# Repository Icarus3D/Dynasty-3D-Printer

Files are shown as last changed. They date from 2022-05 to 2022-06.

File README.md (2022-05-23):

# Dynasty CoreXY 3D Printer
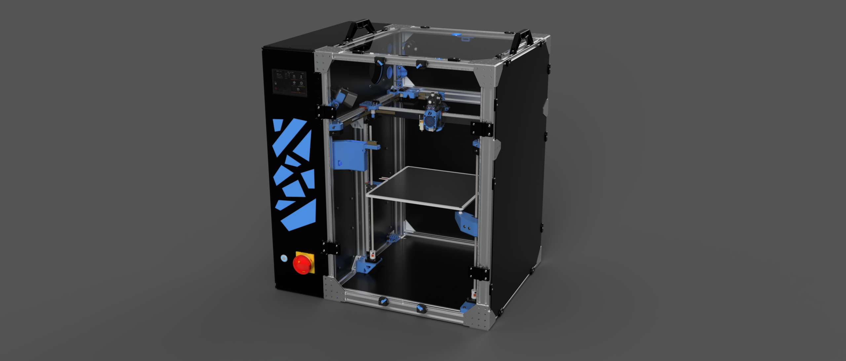
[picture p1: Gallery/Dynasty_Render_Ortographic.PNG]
Dynasty_Final_Render


After having modified my printers a lot and tested several DIY printer kits like Voron and BLV MGN Cube, I wanted a printer that totally met my needs.
I saw printers on the market that could correspond to my needs by modifying them. But I decided to challenge myself by developing my own printer.
After several months of work, here is the result.
This project was originally intended to be personal only, but I thought that making the files open source might motivate other people to start developing their own 3D printer.

:warning: Warning :warning:<br />
This printer is still at the prototype stage and is not optimized. The cost is quite high and the machine also takes a lot of space
If you want to build a 3D printer by yourself, I recommend the [Voron](https://www.vorondesign.com/) or [RatRig](https://v-core.ratrig.com/) printers which have a great community ready to help you.

If you are interested in my work, you can follow me on Instagram [@icarus_3d](https://www.instagram.com/icarus_3d/?hl=fr). I will post news about my future projects in 3D printing.

## Features List
* Print volume 300x300x360mm
* CoreXY kinematic
* Easy maintenance
* Sturdy Structure with 2040 Aluminium Profiles
* Good speed and print quality (Good result at 100mm/s @ 3k accel)
* Accepts spools of 2kg
* Electronic Bay
* Full enclosure
* Direct drive extruder
* Filament fault detector
* Purge Bucket
* Bed thermal expension compensation
* LED strip
* Auto bed leveling
* Access to the printer outside a local network
* Streaming video
* Timelapse
* Automatic power off after print completion

## Frame
Dynasty_3D_Printer
2040 aluminum profiles are used to obtain a rigid structure.
All corners use 3mm aluminum plates coupled with M6 screws directly screwed to the profiles as hidden joints.
The structure is very rigid, but it requires a lot of screws.
The printer, which is very heavy, is about 85cm high.
All electronic components are installed in the electronic bay on the left side of the printer. The panels on the front, bottom, top and back of the electronic bay are 3D printed.
The enclosure is made of transparent and matte black 3mm plexiglass. Except for the plate on which is fixed the electronics, which is 4mm thick.
Thanks to [coldzero.eu](https://www.coldzero.eu/) for the awesome [Custom Dynasty Panels Kit](https://www.coldzero.eu/custom-dynasty-panels).

## Motion System
Dynasty_XY_Carriage
The moving system is an XY core system. The two motors used for the movement of the print head are placed at the back of the printer.
The Y-axis uses two linear rails and the X-axis uses one linear rail fixed on a carbon tube.
The head is moved by a 9mm 2GT belt.

Dynasty_Hotend
The carriage of the hotend is an [EVA](https://main.eva-3d.page/). This is the same carriage platform used for the RatRig printers.

## Bed
Dynasty_Bed
The bed used is a 329x329x6mm cast tooling plate from RatRig.
There is a magnetic plate on top with a flexplate powder coated PEI.
The bed can be heated up to 110°C with a 750W heating pad.
It has three attachment points, each resting on a 3D printed support.
The fixation between the bed and the supports is made with steel balls screwed to the bed and attracted by magnets fixed on the supports.
This system allows to compensate the effects of the thermal expansion of the plate during the heating process. This avoids deformations of the bed caused by the stress. Steel rods guide the balls to ensure the stability of the bed.
The supports are screwed to linear rails and are moved by TR8 lead screws and Nema17 motors. 
These three motors, coupled with the BLTouch sensor, allow the automatic leveling of the bed . There is a link to a [video of the start gcode macro](https://www.youtube.com/watch?v=Yhw2lbUx1_E&t=1s).

## Electronics
Dynasty_Open_Bay
All the electronic components are installed in the electrical bay. Each component is fixed on a 35mm DIN rail with a bracket. The cables are all stored in a 40mm wiring duct.
The electrical bay allows easy access to all electronics and protects the components from the temperature of the printing area.
The printer has a 230V socket at the back. This is directly connected to the emergency stop button on the front panel.
The shutdown button is connected in parallel with the main SSR. Once the printer is switched on with the button, the SSR takes over and the printer can be switched off either via the web interface or directly with the emergency stop button.
The 24V power supply powers the Octopus V1.1 motherboard and the 5V power supply powers the Rapsberry Pi. Most of the components are connected to the motherboard except for the screen and the webcam. The details of the connections are explained in the [Wiring Diagram](https://github.com/Icarus3D/Dynasty-3D-Printer/tree/main/Wiring%20Diagram) folder.

## Firmware
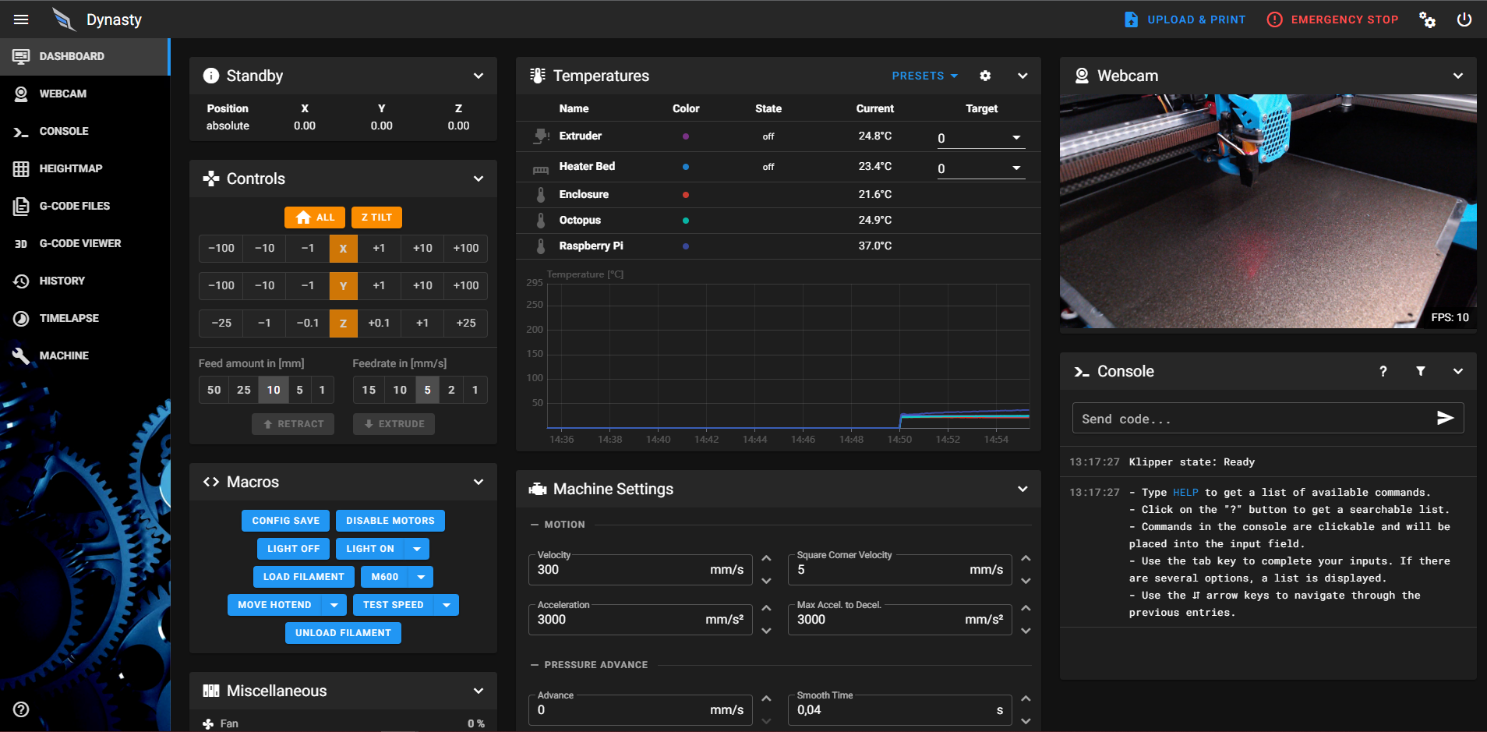
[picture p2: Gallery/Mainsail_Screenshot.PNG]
Mainsail_Screenshot

The printer uses the [Klipper firmware](https://github.com/Klipper3d/klipper).
You can use third-party Moonraker components that allow you to add other functionalities.
Like the [Moonraker timelapse](https://github.com/mainsail-crew/moonraker-timelapse) feature that allows you to make timelapse videos of your prints very easily. This feature was very useful for me to understand the failures of my first prints.
There is also a [Moonraker bot telegram](https://github.com/nlef/moonraker-telegram-bot) that allows you to regularly receive the status of the current print with an image or a short video. If the printing has failed, it is also possible to stop the printing. All this can be done outside the local network.
The user interface used is [Mainsail](https://github.com/mainsail-crew/mainsail). It's an excellent interface with a lot of features and is regularly updated.
All configuration files of the printer are available in the [Firmware](https://github.com/Icarus3D/Dynasty-3D-Printer/tree/main/Firmware) folder.

## Inspirations
The creation of the Dynasty printer was inspired by this open source printers. Thanks to their creator and their community.
* Voron Trident by Voron Design [Github](https://github.com/VoronDesign/Voron-Trident)<br />
* VzBot by Vez3D [Github](https://github.com/VzBoT3D/VzBoT-Vz330)<br />
* RatRig V-Core 3 by RatRig [Github](https://github.com/Rat-Rig/V-core-3)<br />
* BLV MGN Cube by Ben Levi [Web Site](https://www.blvprojects.com/blv-mgn-cube-3d-printer)<br />

## License
The Dynasty 3D printer uses the license [CC BY-NC-SA 4.0](https://creativecommons.org/licenses/by-nc-sa/4.0/)
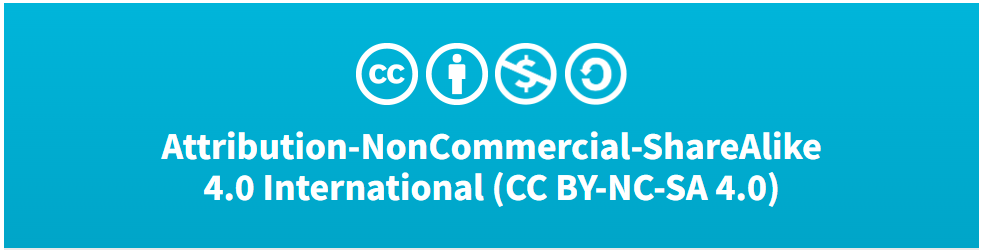
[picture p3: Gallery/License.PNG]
Dynasty_License


:exclamation: All 3D models created by other designers and their remixes used for this printer retain their original license. For more details, see the [3MFs STLs](https://github.com/Icarus3D/Dynasty-3D-Printer/tree/main/3MFs%20STLs) folder. :exclamation:

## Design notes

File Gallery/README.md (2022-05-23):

# Gallery

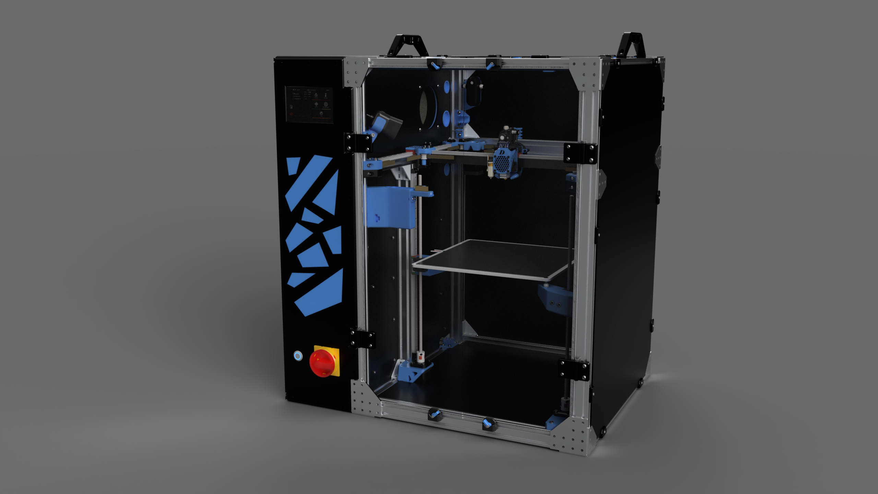
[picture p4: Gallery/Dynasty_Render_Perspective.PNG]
Dynasty_Render_Perspective


Dynasty_Banana_for_Scale

Dynasty_Vase_Mode

[Armadillo Timelapse Video](https://www.youtube.com/watch?v=8Uq6_T-8N7Q)
Armadillo_Print_Sample

[DesertKiss Timelapse Video](https://www.youtube.com/watch?v=NnbRvlF1Fk8)
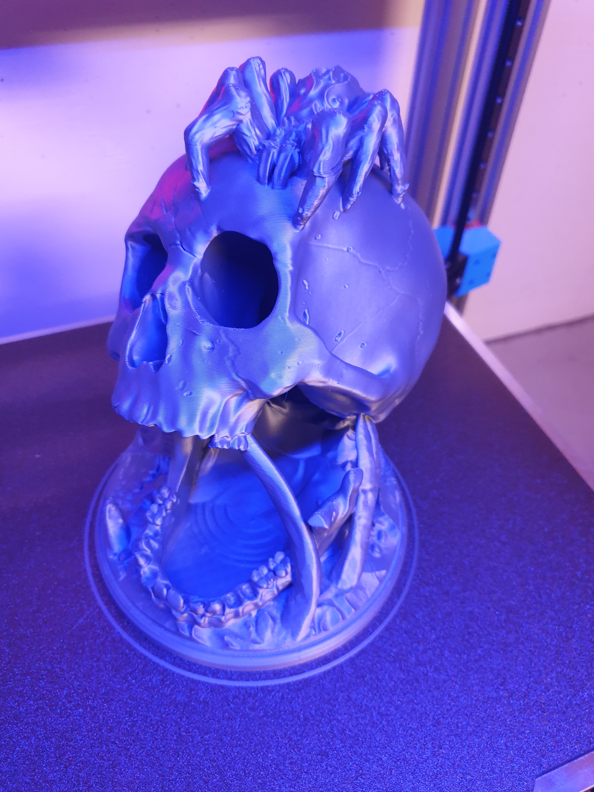
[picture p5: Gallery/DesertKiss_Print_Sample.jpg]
DesertKiss_Print_Sample


[ElfBust Timelapse Video](https://www.youtube.com/shorts/Z34vOpA37Mc)
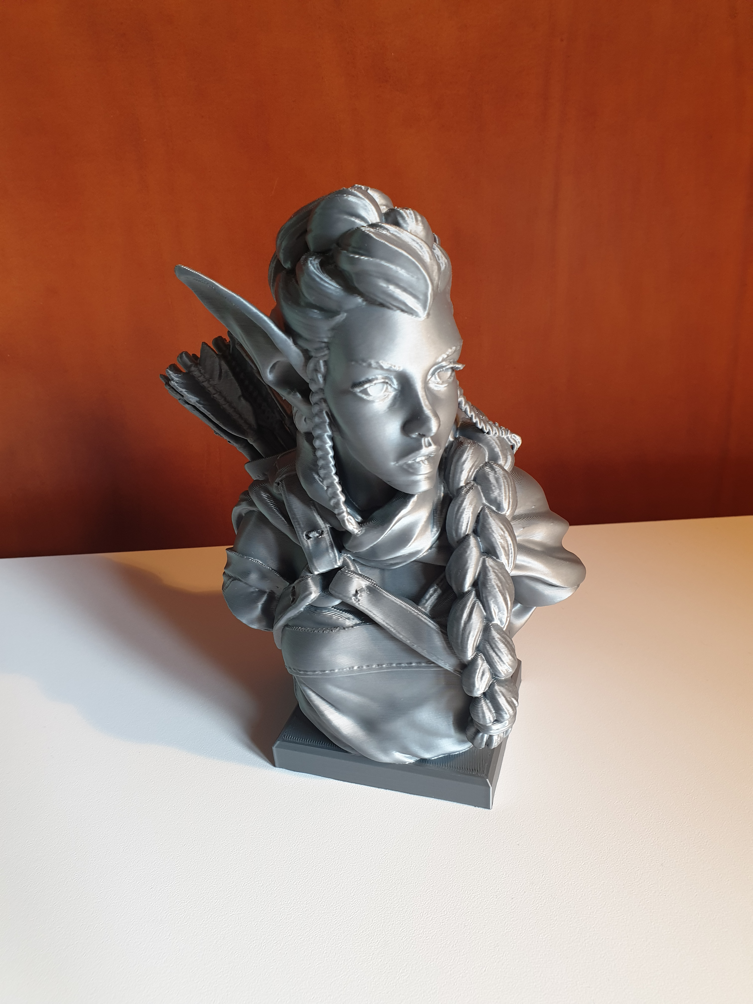
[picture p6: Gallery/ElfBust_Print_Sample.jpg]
ElfBust_Print_Sample


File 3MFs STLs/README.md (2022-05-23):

# .3MF & .STL Files
All files are available in .3MF and .STL format.
Files with the prefix "a_" are printed with the secondary color. Blue is the secondary color of the reference model.
Some files that need to be printed several times have the number of units to be printed as a suffix, for example "_x2".
It is recommended to print the parts used inside the enclosure in ABS or any other equivalent plastic. Other parts that are not sensitive to temperature can be printed in PLA or PETG.
Grommets are the exception. They are printed in TPU A95 to be flexible enough to let the cables pass through.

This printer uses parts made by other designers. Here is a list of these pieces with the details of their remix.
All these files keep their original license.

## DIN Rail Bracket
* a_DIN_Rail_Bracket_Clip_08_Dynasty_Remix_x6.stl<br />
This is a small remix of the [LM2596 Buck Converter Din Bracket](https://www.thingiverse.com/thing:4820100) originally created by 100k3y.
The original was not tight enough on the rail and the brackets were moving along the DIN rail when the printer was moved. To correct this, the distance between the two brackets was reduced by 0.8mm.

## Exhaust Fan Case
* a_fancase-server-bottom-fan-housing.stl
* a_fancase-server-grille.stl
* fancase-server-filter-section.stl<br />
The exhaust fan case [3D Enclosure Extractor Fan with HEPA Carbon filters v2](https://www.printables.com/fr/model/54864-3d-enclosure-extractor-fan-with-hepa-carbon-filter) was made by Colin.
I did not change anything in the original files. I modeled two printed seals in TPU to have a better airtightness.

## Spool Holder
* a_FillerGuideSource_Dynasty_Remix.stl
* a_FillerRollerSource_Dynasty_Remix.stl
* a_FillerWallMountSource_Dynasty_Remix.stl<br />
Remix from the [Filler - The Customizable Filament Holder that fills your printer!](https://www.thingiverse.com/thing:3020026) originally created by HugoHuge.
The roller and the guide has been enlarged to fit a 2.3kg filament spool.
The wall mount has also been modified so that it can be attached to the aluminum profile and panel without touching the other components.

## Door latch
* a_Enclosure_Latch_Left_Dynasty_Remix_x2.stl
* a_Enclosure_Lever_Left_Dynasty_Remix_x2.stl
* Enclosure_Lock_Body_Left_Dynasty_Remix_x2.stl
* a_Enclosure_Latch_Right_Dynasty_Remix_x2.stl
* a_Enclosure_Lever_Right_Dynasty_Remix_x2.stl
* Enclosure_Lock_Body_Right_Dynasty_Remix_x2.stl<br />
This latch originally come from VoronDesign. Unfornately, I have never found the orginals files of VoronDesign. I got them from the VzBot .step files by Vez3D.
The side in contact with the plexiglass door has been enlarged to ensure better adhesion. The shape has been slightly modified to match the size of Motedis aluminum profiles.

## Panel Clip
* Midspan_Panel_Clip_3mm_Dynasty_Remix_x28.stl
* Midspan_Panel_Clip_4mm_Dynasty_Remix_x10.stl<br />
Originals files [midspan_panel_clip_3mm_x12.stl](https://github.com/VoronDesign/Voron-1/blob/Voron1.8/STLs/Panel_Mounting/midspan_panel_clip_3mm_x12.stl) were made by VoronDesign.
The 3mm version has been slightly modified to have a tighter fit and does not touch the 3D printed panels of the electronic bay.
The 4mm version is based on the 3mm and used for the 4mm electronic panel. The dimensions have been adapted for the 4mm panel and prevent the clip from touching the 3D printed panels.

## Handle
* VzBoT_Handle_Dynasty_Remix_x2.stl<br />
Remix of VzBot handle [handle.stl](https://github.com/VzBoT3D/VzBoT-Vz330/blob/master/Assemblies%20BOM%20and%20STL/Frame/STLs/handle.stl) originally created by Vez3D.
The handles have been raised a few millimeters to facilitate access to the handles near the panels.

## Hotend
* a_shroud_dynasty_remix.stl
* top_orbiter_mgn12_dynasty_remix.stl
* etc...<br />
All the files of the 3D carriage platform of this printer were created by the [EVA](https://main.eva-3d.page/) team.
A grid has been added to the shroud to protect the fan. The edges have been shortened to allow the addition of an ADXL345 accelerometer. 
Two holes were added to the top orbiter mgn12 to put two M2.5 inserts wich allow to fix the accelerometer.

## Wires Holder
* Frame_Wires_Holder.stl<br />
This [Frame Wires Holder](https://www.blvprojects.com/post/beta-test-frame-wires-holder) were made by Ben Levi.
They have not been modified.

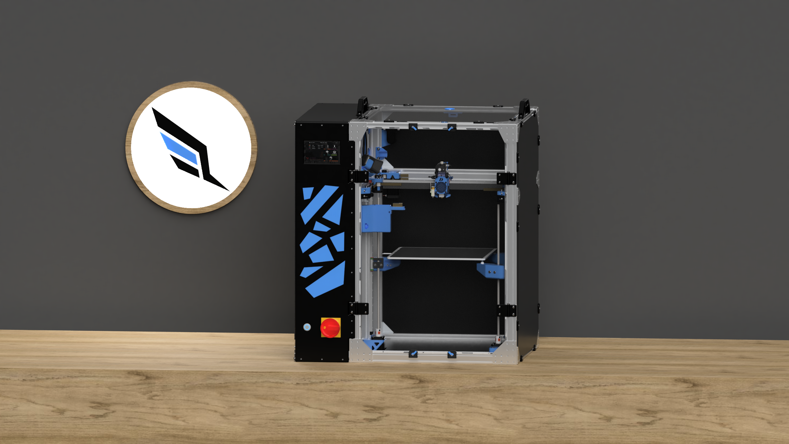
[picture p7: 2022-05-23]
Gallery/Dynasty_Scene_Ortographic2.PNG

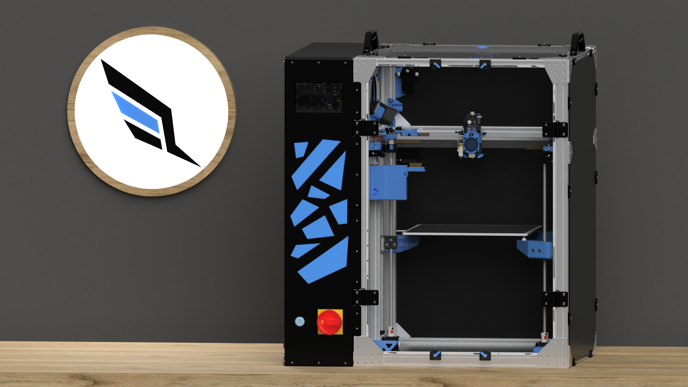
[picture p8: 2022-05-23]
Gallery/Dynasty_Scene_Ortographic.PNG

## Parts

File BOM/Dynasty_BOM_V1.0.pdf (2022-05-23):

Dynasty_BOM_Rev1.0

Page 1

Category | Subcategory | Component | Quantity | Price per Unit | Price | Link
Printed Parts | Filament | Primary Color (Black) | 1 | 28.40 USD | 28.40 USD | Fiberlogy ABS+ (https://www.3djake.ch/fr-CH/fiberlogy/abs-plus-black)
| | Secondary Color (Blue) | 1 | 28.40 USD | 28.40 USD | Fiberlogy ABS+ (https://www.3djake.ch/fr-CH/fiberlogy/abs-plus-blue)
Frame | Structure | Aluminum Profile 2020 Type B Slot 6 180mm | 4 | 1.06 USD | 4.24 USD | Motedis (https://www.motedis.ch/shop/Profile-a-rainures/Profile-aluminium-20x20-Type-B-rainure-6::999991.html)
| | Aluminum Profile 2040 Type B Slot 6 480mm | 5 | 4.82 USD | 24.10 USD | Motedis (https://www.motedis.ch/shop/Profile-a-rainures/Profile-aluminium-20x40-Type-B-rainure-6::99999158.html)
| | Aluminum Profile 2040 Type B Slot 6 520mm | 6 | 5.22 USD | 31.32 USD | Motedis (https://www.motedis.ch/shop/Profile-a-rainures/Profile-aluminium-20x40-Type-B-rainure-6::99999158.html)
| | Aluminum Profile 2040 Type B Slot 6 530mm | 2 | 5.32 USD | 10.64 USD | Motedis (https://www.motedis.ch/shop/Profile-a-rainures/Profile-aluminium-20x40-Type-B-rainure-6::99999158.html)
| | Aluminum Profile 2040 Type B Slot 6 800mm | 4 | 8.03 USD | 32.12 USD | Motedis (https://www.motedis.ch/shop/Profile-a-rainures/Profile-aluminium-20x40-Type-B-rainure-6::99999158.html)
| Feet | Threaded Rod M6x40 for Ball Feet, Steel, Series 10 | 4 | 1.12 USD | 4.48 USD | Motedis (https://www.motedis.ch/shop/Base-mechaniques/Pieds-reglables-et-accessoires/Pied-reglable-en-piece-detachee/Articles-Elements-etage-serie-10-PA/Articles-Eleme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)
| | Base 40 for Adjustable Feet, PA, Series 10 | 4 | 1.43 USD | 5.71 USD | Motedis (https://www.motedis.ch/shop/Base-mechaniques/Pieds-reglables-et-accessoires/Pied-reglable-en-piece-detachee/Articles-Elements-etage-serie-10-PA/Articles-Eleme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)
| | Anti-slip Plate 40 for Adjustable Feet, Series 10 | 4 | 1.27 USD | 5.07 USD | Motedis (https://www.motedis.ch/shop/Base-mechaniques/Pieds-reglables-et-accessoires/Pied-reglable-en-piece-detachee/Articles-Elements-etage-serie-10-PA/Articles-Eleme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)
| Plate | Plate L 2020 3mm 5 Holes | 4 | 1.16 USD | 4.63 USD | Motedis (https://www.motedis.ch/shop/Profile-accessoires/Plaques-de-connexion/Plaque-de-connexion-en-L-58x58x3-Decoupe-au-laser::999993868.html)
| | Plate L 2040 4mm 7 Holes | 8 | 0.96 USD | 7.68 USD | Aliexpress (https://fr.aliexpress.com/item/32649078057.html?cn=e-c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)
| | Plate L 4040 3mm 12 Holes | 8 | 1.57 USD | 12.60 USD | Motedis (https://www.motedis.ch/shop/Profile-accessoires/Plaques-de-connexion/Plaque-de-connexion-en-L-78x78x3-Decoupe-au-laser::999993853.html)
| | Plate T 2020 3mm 5 Holes | 4 | 1.16 USD | 4.63 USD | Motedis (https://www.motedis.ch/shop/Profile-accessoires/Plaques-de-connexion/Plaque-de-connexion-en-T-58x58x3-Decoupe-au-laser-serie-20::999993776.html)
| | Plate T 4040 3mm 12 Holes | 2 | 1.54 USD | 3.09 USD | Motedis (https://www.motedis.ch/shop/Profile-accessoires/Plaques-de-connexion/Plaque-de-connexion-en-T-78x78x3-Decoupe-au-laser::999993857.html)
| Bracket | Bracket 2020 B-Type Slot 6 (with fixing kit) | 13 | 1.44 USD | 18.72 USD | Motedis (https://www.motedis.ch/shop/Profile-accessoires/Bracket-for-Aluminium-profiles/Equerre-dassemblage-20x20-B-type-rainure-6::999991062.html)
| | Bracket 2040 B-Type Slot 6 (with fixing kit) | 19 | 2.37 USD | 45.03 USD | Motedis (https://www.motedis.ch/shop/Profile-accessoires/Bracket-for-Aluminium-profiles/Equerre-dassemblage-20x40-B-type-rainure-6::99999554.html)
| Panels | Dynasty Panels Kit 3mm & 4mm | 1 | 220.10 USD | 220.10 USD | Coldzero (https://www.coldzero.eu/custom-dynasty-panels)
Motion System | XY axe | Carbon fiber tube 20x20x18 500mm | 1 | 11.50 USD | 11.50 USD | Aliexpress (https://fr.aliexpress.com/item/32946654825.html?spm=a2g0s.9042311.0.0.3e6e6c37yhnRV5)
| | MGN12H 400mm linear rail Z1 preloaded block | 3 | 65.00 USD | 195.00 USD | Aliexpress (https://www.aliexpress.com/item/4000799585801.html?spm=a2g0o.cart.0.0.68773c00W9mmQ3&mp=1)
| | | 1 | 18.80 USD | 18.80 USD
| | Idler Pulley - Smooth for 2GT-20T - 9mm Belt - 5mm Bore (Compressible) | 8 | 4.30 USD | 34.40 USD | RatRig (https://www.ratrig.com/idler-pulley-gt-20t-profile-smooth-multiple-sizes-and-types.html)
| | Idler Pulley - Toothed for 2GT-20T - 9mm Belt - 5mm Bore (Compressible) | 2 | 4.45 USD | 8.90 USD | RatRig (https://www.ratrig.com/idler-pulley-toothed-for-2gt-20t-5mm-bore-multiple-sizes-and-types.html)
| | Timing Pulley - 2GT (2mm) - 20 Tooth - For 9mm Belt | 2 | 2.16 USD | 4.32 USD | RatRig (https://www.ratrig.com/openbuilds-gt2-2mm-aluminum-timing-pulley-9mm.html)
| | High Torque Nema17 Motor 0.9° | 5 | 15.92 USD | 79.60 USD | E3D (https://e3d-online.com/products/motors)
| Z axe | MGN12H 450mm linear rail Z1 preloaded block | 3 | 71.40 USD | 214.20 USD | Aliexpress (https://www.aliexpress.com/item/4000799585801.html?spm=a2g0o.cart.0.0.68773c00W9mmQ3&mp=1)
| | Lead Screw Flexible Coupler | 3 | 4.87 USD | 14.61 USD | Aliexpress (https://fr.aliexpress.com/item/33011094528.html)
| | Lead Screw T8 PTFE 450mm | 3 | 16.84 USD | 50.52 USD | Aliexpress (https://fr.aliexpress.com/item/1005002055526955.html)
| | Anti-Backlash Nut Block for 8mm Lead Screw | 3 | 5.79 USD | 17.37 USD | RatRig (https://www.ratrig.com/anti-backlash-nut-block-for-8mm-metric-acme-lead-screw.html)
| | Thrust Bearing F8-16M | 3 | 1.83 USD | 5.49 USD | RatRig (https://www.ratrig.com/thrust-bearing-f8-16m.html)
| Bed | FlexPlate Powder Coated PEI 310x310mm | 1 | 51.98 USD | 51.98 USD | RatRig (https://www.ratrig.com/flexplate-set-pei-310-x-310-mm.html)
| | Bed Plate 329*329*6mm | 1 | 58.68 USD | 58.68 USD | RatRig (https://www.ratrig.com/bed-plate-cast-tooling-plate-pre-machined-multiple-sizes.html)
| | Aluminium Spacer 6mm | 3 | 0.24 USD | 0.72 USD | RatRig (https://www.ratrig.com/aluminium-spacer-6mm.html)
| | Steel Ball 12mm M5 | 3 | 1.05 USD | 3.15 USD | RatRig (https://www.ratrig.com/steel-ball-12mm-threaded-m5.html)
| | Dowel Pin 3x35mm | 6 | 0.42 USD | 2.52 USD | RatRig (https://www.ratrig.com/dowel-pin-3-0mm-x-35-0mm.html)
| | Magnet 20x10x5mm Two hole M3 | 3 | 2.10 USD | 6.30 USD | RatRig (https://www.ratrig.com/magnet-20-x-10-x-5mm-two-hole-m3-countersink-screws.html)
Electric | Hotend | Dragon High Flow Hotend | 1 | 80.11 USD | 80.11 USD | Aliexpress (https://fr.aliexpress.com/item/1005002629698126.html)
| | Orbiter Extruder V1.5 | 1 | 55.18 USD | 55.18 USD | Aliexpress (https://fr.aliexpress.com/item/1005002029267359.html?spm=a2g0s.9042311.0.0.3e6e6c37yhnRV5)
| | Sunon 4010 12V Fan | 1 | 4.62 USD | 4.62 USD | Digikey (https://www.digikey.ch/product-detail/fr/MF40101VX-1000U-A99/259-1798-ND/6198736?itemSeq=373298864)
| | Sunon 5015 12V Fan | 1 | 8.51 USD | 8.51 USD | Digikey (https://www.digikey.ch/product-detail/fr/sunon-fans/MF50151VX-B00U-A99/259-1829-ND/7691033)
| | Heater Cartridge 24V 40W | 1 | 1.94 USD | 1.94 USD | Aliexpress (https://fr.aliexpress.com/item/32815934251.html)
| | Semitec 104GT-2 ATC thermistor | 2 | 2.34 USD | 4.68 USD | Aliexpress (https://fr.aliexpress.com/item/32847452724.html)
| | Omron Endstop | 2 | 2.98 USD | 5.96 USD | Digikey (https://www.digikey.ch/de/products/detail/omron-electronics-inc-emc-div/SS-5GL2/137204)
| | BLTouch | 1 | 42.10 USD | 42.10 USD | 3Djake (https://www.3djake.ch/fr-CH/antclabs/capteur-de-nivellement-bltouch)
| | Accelerometer ADXL345 | 1 | 21.00 USD | 21.00 USD | Distrelec (https://www.distrelec.ch/fr/adxl345-trois-axes-capteur-acceleration-5v-adafruit-1231/p/30139029)
| | PFA Tube 2m | 1 | 8.84 USD | 8.84 USD | Aliexpress (https://fr.aliexpress.com/item/33030078259.html)
| Bed | C-LIN SSR 40A | 1 | 22.01 USD | 22.01 USD | RatRig (https://www.ratrig.com/clin-ssr-40a-relay.html)
| | Silicone Heater Bed Pad 280x280mm 220V 600W | 1 | 66.50 USD | 66.50 USD | RatRig (https://www.ratrig.com/keenovo-heater-pad-and-ssr-relays-multiple-sizes-configurations.html)
| | Thermal Fuse 15A 125°C | 1 | 3.09 USD | 3.09 USD | Aliexpress (https://fr.aliexpress.com/item/32885492280.html)
| Electronics | Shurter Plug C14 250V | 1 | 4.36 USD | 4.36 USD | Distrelec (https://www.distrelec.ch/fr/fiche-pour-appareils-c14-250v-schurter-6200-2200/p/14358747)
| | Metal Switch 22mm 220V Self-Reset | 1 | 3.33 USD | 3.33 USD | Aliexpress (https://fr.aliexpress.com/item/4001246312476.html)
| | Cable Socket 22mm | 1 | 1.14 USD | 1.14 USD | Aliexpress (https://fr.aliexpress.com/item/4001291947746.html)
| | Eaton Emergency Switch | 1 | 41.93 USD | 41.93 USD | Distrelec (https://www.distrelec.ch/fr/interrupteur-principal-arret-urgence-eaton-t0-8200-ea-svb/p/13511931)
| | Crouzet SSR 50A | 1 | 56.88 USD | 56.88 USD | Digikey (https://www.digikey.ch/de/products/detail/crouzet/84137120N/13175957)
| | CUI Inc. 24V Power Supply VGS-320D-24-B | 1 | 55.55 USD | 55.55 USD | Digikey (https://www.digikey.ch/de/products/detail/cui-inc/VGS-320D-24-B/13690525)
| | DC/DC Converter DIN Rail 5V 3A | 1 | 25.09 USD | 25.09 USD | Distrelec (https://www.distrelec.ch/fr/convertisseur-dc-dc-pour-rail-din-5v-3a-15w-reglable-mean-well-ddr-15g/p/30134120)
| | BTT Octopus V1.1 Motherboard with TMC2209 | 1 | 67.63 USD | 67.63 USD | Aliexpress (https://fr.aliexpress.com/item/1005002611654405.html)

## Bill of Materials for Dynasty 3D Printer [V1.0 10.05.2022]

Belt 2GT 9mm – 600mm | RatRig (https://www.ratrig.com/gt2-timing-belt-1mt.html) | Aliexpress (https://fr.aliexpress.com/item/32853559638.html)

Dynasty_BOM_Rev1.0

Page 2

| | Younuon 6010 Fan 24V | 1 | 8.97 USD | 8.97 USD | Aliexpress (https://fr.aliexpress.com/item/4000233226859.html)
| | BTT Smart Filament Sensor | 1 | 11.52 USD | 11.52 USD | Aliexpress (https://fr.aliexpress.com/item/4000269547406.html)
| | Noctua NF-F12 iPPC-2000 | 1 | 34.50 USD | 34.50 USD | LDLC (https://www.ldlc.com/fr-ch/fiche/PB00169917.html)
| | Hepa Cover Filter Set Zortrax | 1 | 36.85 USD | 36.85 USD | 3Djake (https://www.3djake.ch/fr-CH/zortrax/hepa-cover-filter-set)
| | LED Strip RGBNW 1m 60 IP65 White PCB | 1 | 9.37 USD | 9.37 USD | Aliexpress (https://fr.aliexpress.com/item/32476317187.html?mp=1)
| | Raspberry Pi 3 B+ | 1 | 43.42 USD | 43.42 USD | Mouser (https://www.mouser.ch/ProductDetail/Raspberry-Pi/RPI3-MODBP-BULK?qs=gTYE2QTfZfTS/nQn9798dg==)
| | Winsinn 4010 fan 24V | 1 | 2.41 USD | 2.41 USD | Aliexpress (https://fr.aliexpress.com/item/1005003878405207.html)
| | 0.5m USB Cable | 1 | 2.69 USD | 2.69 USD | Aliexpress (https://fr.aliexpress.com/item/32678087225.html)
| | Flexible Cable 1m Raspebrry Pi | 1 | 0.53 USD | 0.53 USD | Aliexpress (https://fr.aliexpress.com/item/1005001636578419.html)
| | BTT PI TFT50 Screen | 1 | 47.15 USD | 47.15 USD | Aliexpress (https://fr.aliexpress.com/item/1005001270623489.html)
| | Logitech Streamcam | 1 | 125.00 USD | 125.00 USD | Digitec (https://www.digitec.ch/fr/s1/product/logitech-streamcam-2-mpx-webcams-12926543?supplier=406802)
| | Adapter USB 3.0 to USB-C | 1 | 9.20 USD | 9.20 USD | Digitec (https://www.digitec.ch/fr/s1/product/exsys-ex-47991-usb-30-370-cm-adaptateurs-pour-notebook-6037208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)
| Mounting | Wiring Duct 40x40mm 2m | 1 | 16.05 USD | 16.05 USD | Distrelec (https://www.distrelec.ch/fr/chemins-de-cables-heladuct-40-40mm-2m-pvc-gris-hellermanntyton-htwd-pw-40x40-pvc-gy/p/30119358)
| | Rail DIN omega 1m 35x7.5mm | 2 | 4.50 USD | 9.00 USD | Distrelec (https://www.distrelec.ch/fr/rail-din-omega-1m-35x7-5mm-rnd-connect-rnd-465-00766/p/30119896)
| | SSR DIN Rail Clamp | 2 | 2.26 USD | 4.52 USD | Aliexpress (https://fr.aliexpress.com/item/32865553893.html?mp=1)
| | Self-closing braided wire sheath | 2 | 2.70 USD | 5.40 USD | Aliexpress (https://fr.aliexpress.com/item/4000284383278.html)
| | Bearing 608 | 1 | 5.01 USD | 5.01 USD | Aliexpress (https://fr.aliexpress.com/item/32956652613.html?pdp_ext_f=%7B%22sku_id%22:%2266485988816%22%7D)
Fasterners | Set | Set Insert M2,M3,M4,M5 | 1 | 11.33 USD | 11.33 USD | Aliepxress (https://fr.aliexpress.com/item/4000023033943.html)
| | Set M3 SHCS Screws & Nuts | 1 | 17.82 USD | 17.82 USD | Aliexpress (https://fr.aliexpress.com/item/4001345484717.html)
| | Set M2,M3,M4,M5 BHCS Screws, Shim & Nuts 880 | 1 | 24.54 USD | 24.54 USD | Aliexpress (https://fr.aliexpress.com/item/33033655207.html)
| | Set M2,M3,M4,M5 SHCS Screws, Shim & Nuts 880 | 1 | 25.66 USD | 25.66 USD | Aliexpress (https://fr.aliexpress.com/item/33033655207.html)
| | Set M2,M3,M4,M5 FHCS Screws, Shim & Nuts 880 | 1 | 23.43 USD | 23.43 USD | Aliexpress (https://fr.aliexpress.com/item/33033655207.html)
| M2 | M2x10 SHCS | 2 | 0.64 USD | 1.28 USD | Aliexpress (https://fr.aliexpress.com/item/33046502668.html)
| | | 12 | 0.00 USD | 0.00 USD
| | | 3 | 0.00 USD | 0.00 USD
| | | 2 | 0.00 USD | 0.00 USD
| | M3x8 SHCS | 134 | 0.14 USD | 18.14 USD | Motedis (https://www.motedis.ch/shop/Base-mechaniques/DIN-standard-elements/Vis-DIN-7380::999991070.html)
| | M3x10 SHCS | 8 | 0.00 USD | 0.00 USD | Set M3 SHCS Screws & Nuts
| | M3x12 SHCS | 32 | 0.05 USD | 1.63 USD | Aliexpress (https://fr.aliexpress.com/item/33046502668.html)
| | M3x16 SHCS | 12 | 0.00 USD | 0.00 USD | Set M3 SHCS Screws & Nuts
| | M3x20 SHCS | 12 | 0.00 USD | 0.00 USD | Set M3 SHCS Screws & Nuts
| | M3x30 SHCS | 2 | 0.00 USD | 0.00 USD | Set M3 SHCS Screws & Nuts
| | M3x40 SHCS | 12 | 0.00 USD | 0.00 USD | Set M3 SHCS Screws & Nuts
| | | 3 | 0.00 USD | 0.00 USD
| | | 2 | 0.00 USD | 0.00 USD
| | M3 T Nut | 148 | 0.05 USD | 6.85 USD | Aliexpress (https://fr.aliexpress.com/item/32814359094.html)
| | | 30 | 0.00 USD | 0.00 USD
| | | 8 | 0.00 USD | 0.00 USD
| | | 4 | 0.00 USD | 0.00 USD
| | | 4 | 0.00 USD | 0.00 USD
| | | 8 | 0.00 USD | 0.00 USD
| | | 12 | 0.00 USD | 0.00 USD
| M5 | M5x8 BHCS | 300 | 0.14 USD | 40.62 USD | Motedis (https://www.motedis.ch/shop/Base-mechaniques/DIN-standard-elements/Vis-DIN-7380::999991070.html)
| | M5x10 BHCS | 34 | 0.14 USD | 4.60 USD | Motedis (https://www.motedis.ch/shop/Base-mechaniques/DIN-standard-elements/Vis-DIN-7380::999991070.html)
| | M5x12 BHCS | 20 | 0.14 USD | 2.71 USD | Motedis (https://www.motedis.ch/shop/Base-mechaniques/DIN-standard-elements/Vis-DIN-7380::999991070.html)
| | M5x16 BHCS | 22 | 0.14 USD | 2.98 USD | Motedis (https://www.motedis.ch/shop/Base-mechaniques/DIN-standard-elements/Vis-DIN-7380::999991070.html)
| | | 4 | 0.00 USD | 0.00 USD
| | M5x16 SHCS | 16 | 0.16 USD | 2.60 USD | Motedis (https://www.motedis.ch/shop/Base-mechaniques/DIN-standard-elements/Vis-DIN-912::999991121.html)
| | | 5 | 0.00 USD | 0.00 USD
| | M5x30 SHCS | 8 | 0.16 USD | 1.30 USD | Motedis (https://www.motedis.ch/shop/Base-mechaniques/DIN-standard-elements/Vis-DIN-912::999991121.html)
| | M5x35 SHCS | 2 | 0.16 USD | 0.32 USD | Motedis (https://www.motedis.ch/shop/Base-mechaniques/DIN-standard-elements/Vis-DIN-912::999991121.html)
| | M5x40 SHCS | 10 | 0.16 USD | 1.62 USD | Motedis (https://www.motedis.ch/shop/Base-mechaniques/DIN-standard-elements/Vis-DIN-912::999991121.html)
| | M5x45 SHCS | 8 | 0.16 USD | 1.30 USD | Motedis (https://www.motedis.ch/shop/Base-mechaniques/DIN-standard-elements/Vis-DIN-912::999991121.html)
| | | 4 | 0.00 USD | 0.00 USD
| | | 18 | 0.00 USD | 0.00 USD
| | M5 T Nut B-Slot Type 6 | 424 | 0.19 USD | 80.35 USD | Motedis (https://www.motedis.ch/shop/Profile-accessoires/Dans-la-rainure/Ecrou-a-tete-marteau-B-Type-rainure-6-M5::999997145.html)
| | | 43 | 0.00 USD | 0.00 USD
| | Mini Precision Shim M5 | 20 | 0.26 USD | 5.20 USD | RatRig (https://www.ratrig.com/precision-mini-shim-8x5x1mm.html)
| M6 | M6x16 BHCS | 48 | 0.14 USD | 6.50 USD | Motedis (https://www.motedis.ch/shop/Base-mechaniques/DIN-standard-elements/Vis-DIN-7380::999991070.html)
| | | | Total: | 2,501.83 USD
M3 | M3x8 BHCS | Set M2,M3,M4,M5 BHCS Screws, Shim & Nuts
| M3x12 BHCS | Set M2,M3,M4,M5 BHCS Screws, Shim & Nuts
| M3x20 BHCS | Set M2,M3,M4,M5 BHCS Screws, Shim & Nuts
| M3x12 FHCS | Set M2,M3,M4,M5 FHCS Screws, Shim & Nuts 880
| M3x20 FHCS | Set M2,M3,M4,M5 FHCS Screws, Shim & Nuts 880
| M3 Nut | Set M2,M3,M4,M5 SHCS Screws, Shim & Nuts 880
M4 | M4x12 BHCS | Set M2,M3,M4,M5 BHCS Screws, Shim & Nuts 880
| M4x20 BHCS | Set M2,M3,M4,M5 BHCS Screws, Shim & Nuts 880
| M4x8 SHCS | Set M2,M3,M4,M5 SHCS Screws, Shim & Nuts 880
| M4 Shim | Set M2,M3,M4,M5 SHCS Screws, Shim & Nuts 880
| M4 Nut | Set M2,M3,M4,M5 SHCS Screws, Shim & Nuts 880
M5x12 SHCS | Set M2,M3,M4,M5 SHCS Screws, Shim & Nuts 880
M5x20 SHCS | Set M2,M3,M4,M5 SHCS Screws, Shim & Nuts 880
M5x16 FHCS | Set M2,M3,M4,M5 FHCS Screws, Shim & Nuts 880
M5 Shim | Set M2,M3,M4,M5 SHCS Screws, Shim & Nuts 880
M5 Nut | Set M2,M3,M4,M5 SHCS Screws, Shim & Nuts 880

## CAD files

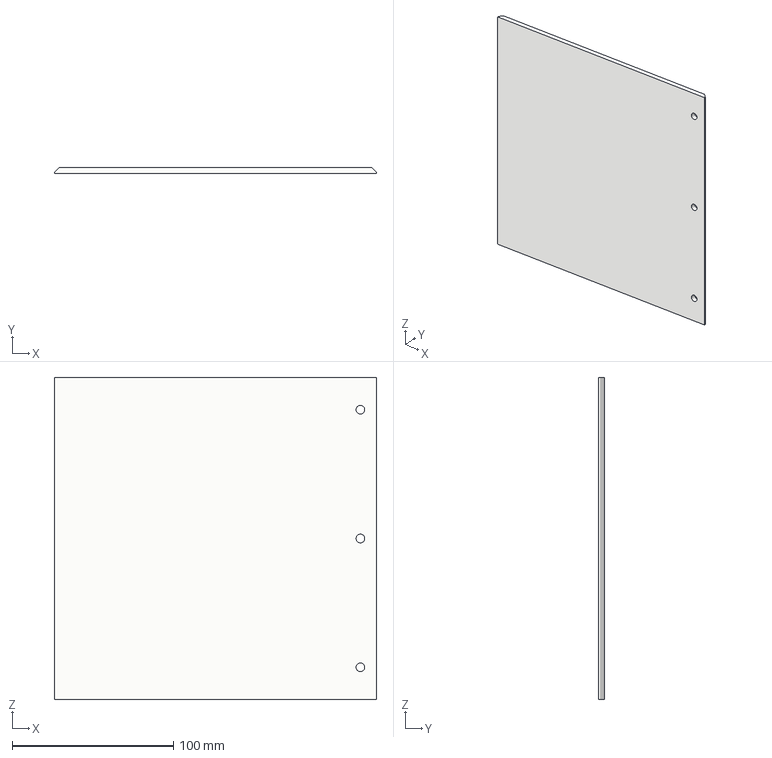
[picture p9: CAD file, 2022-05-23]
3MFs STLs/Electronics_Bay/3D_Panel/Back_3D_Panel/Back_3D_Panel_Part3.3mf
200.0 x 4.00 x 200.0 mm

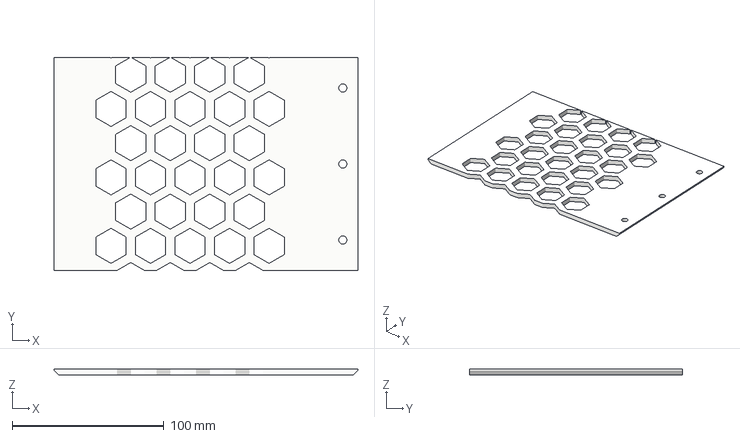
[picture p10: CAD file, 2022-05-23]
3MFs STLs/Electronics_Bay/3D_Panel/Bot_3D_Panel/Bot_3D_Panel_Part2.3mf
200.0 x 140.0 x 4.00 mm

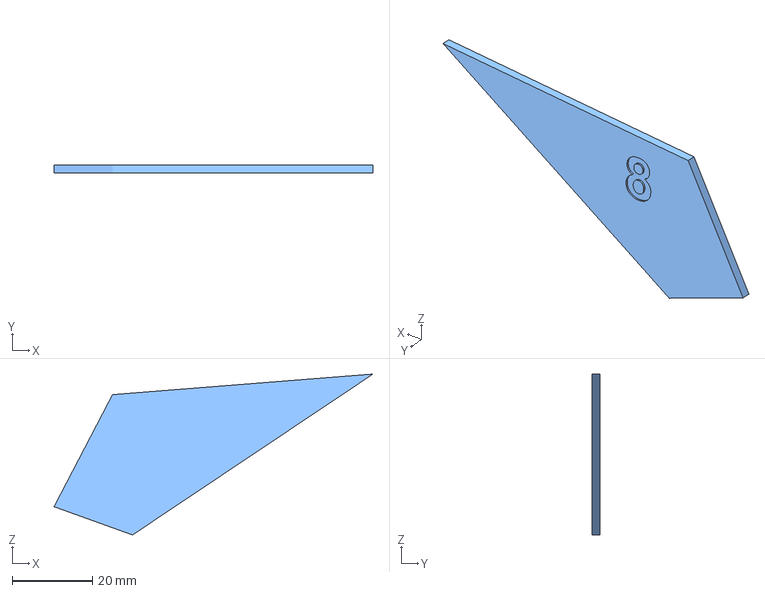
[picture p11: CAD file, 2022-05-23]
3MFs STLs/Electronics_Bay/3D_Panel/Front_3D_Panel/a_Front_3D Panel_Blue_Plate8.3mf
79.6 x 2.00 x 40.1 mm

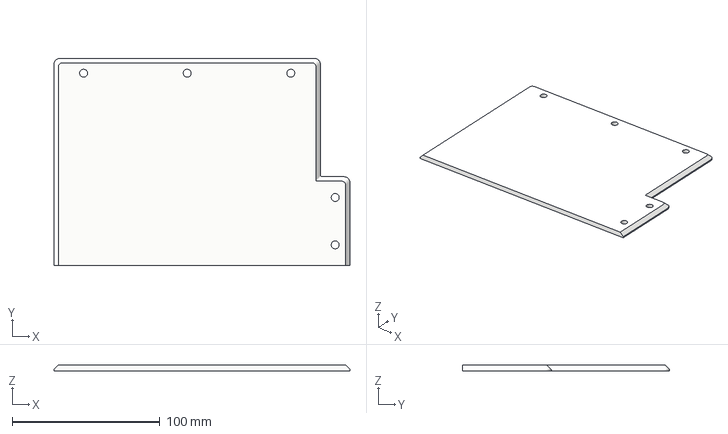
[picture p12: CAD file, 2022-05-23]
3MFs STLs/Electronics_Bay/3D_Panel/Top_3D_Panel/Top_3D_Panel_Part1.3mf
200.0 x 140.0 x 4.00 mm

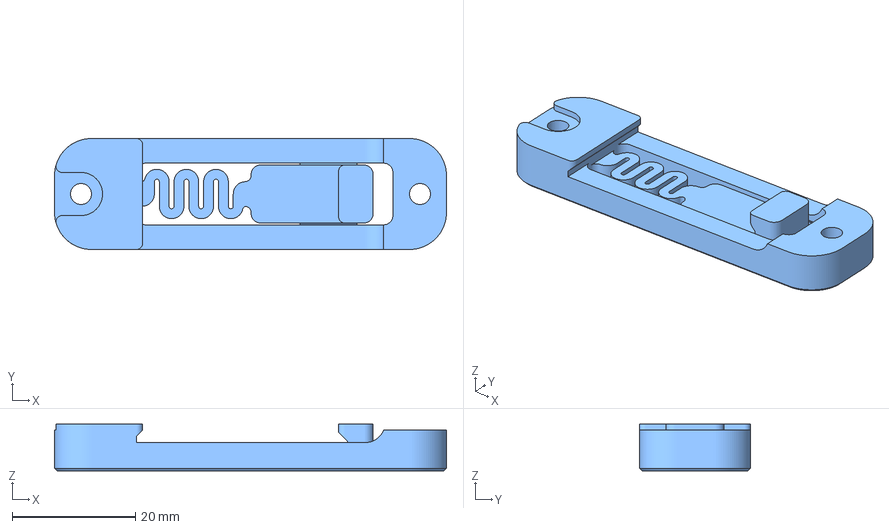
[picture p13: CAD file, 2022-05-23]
3MFs STLs/Electronics_Bay/a_DIN_Rail_Bracket_Clip_08_Dynasty_Remix_x6.3mf
63.6 x 18.0 x 7.60 mm

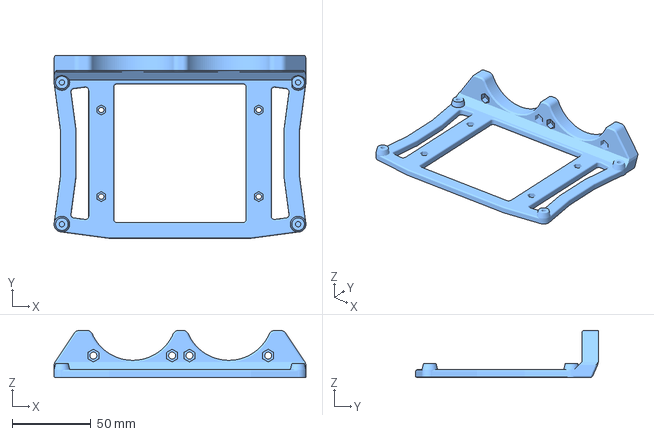
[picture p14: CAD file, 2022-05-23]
3MFs STLs/Electronics_Bay/BTT_Octopus_Board_Mount/a_BTT_Octopus_Board_Mount.3mf
160.0 x 116.0 x 30.0 mm

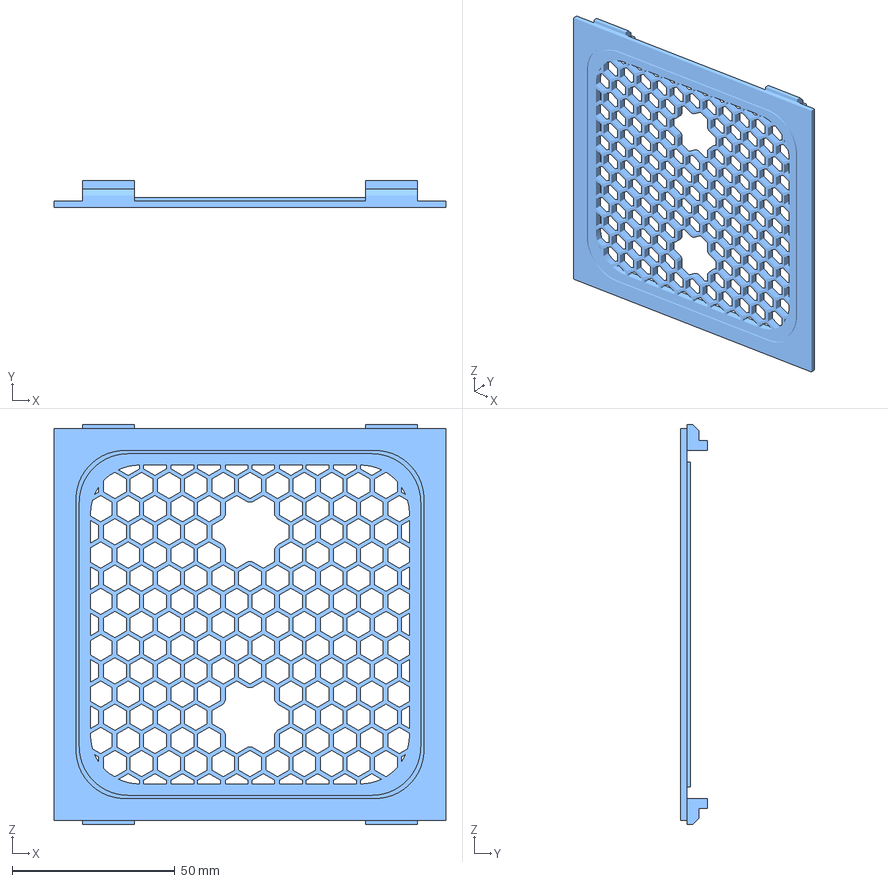
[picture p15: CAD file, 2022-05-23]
3MFs STLs/Electronics_Bay/Exhaust_Fan_Case/a_fancase-server-grille.3mf
120.5 x 8.20 x 123.0 mm

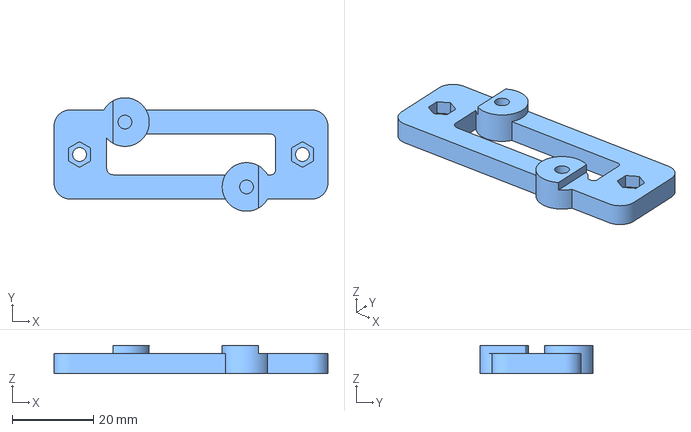
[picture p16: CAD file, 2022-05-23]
3MFs STLs/Electronics_Bay/LM2596_Converter_Mount/a_LM2596_Converter_Mount.3mf
67.6 x 28.0 x 7.00 mm

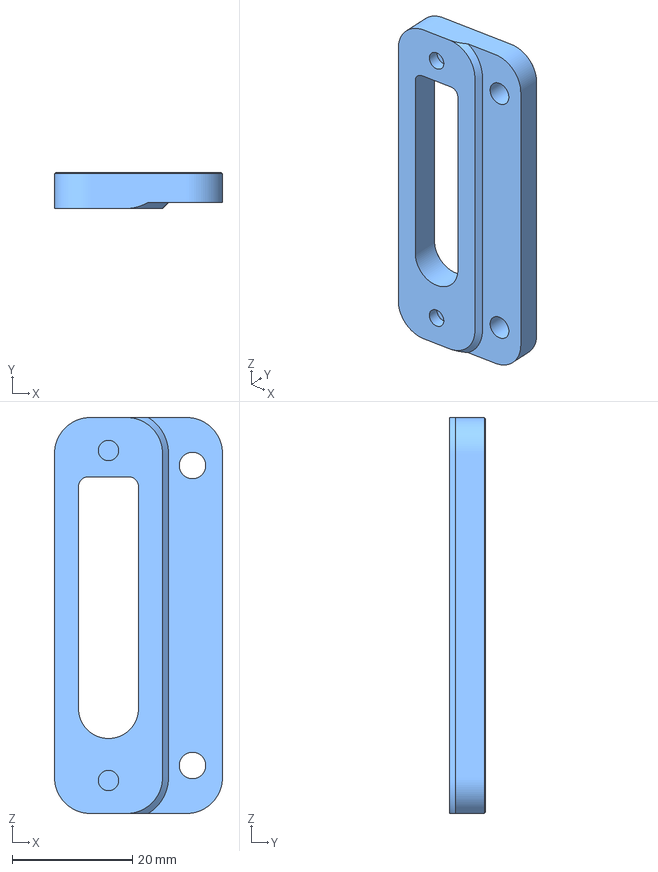
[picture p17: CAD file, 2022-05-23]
3MFs STLs/Electronics_Bay/PSU_Mount/a_PSU_Mount2.3mf
28.0 x 6.00 x 66.0 mm

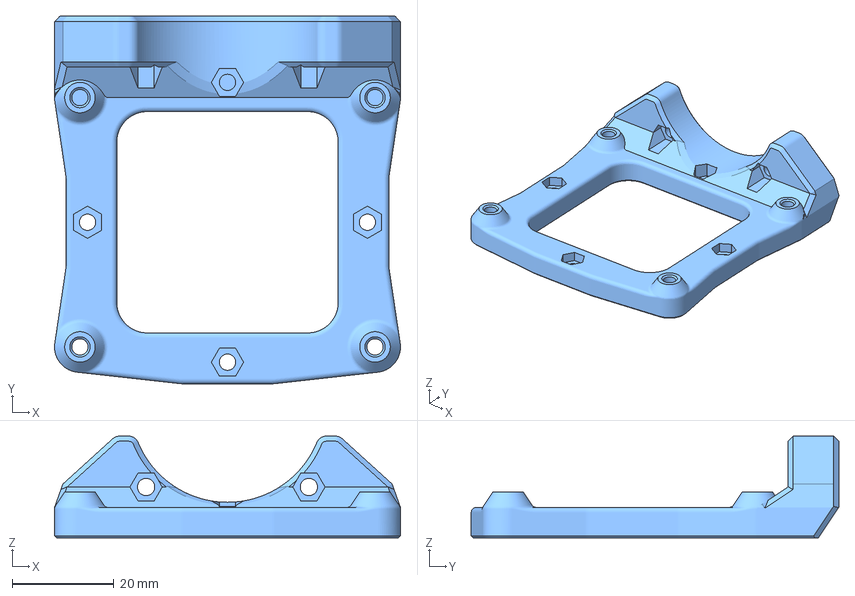
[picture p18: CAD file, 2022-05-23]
3MFs STLs/Electronics_Bay/Raspberry_Pi_Mount/a_Raspberry_Pi_Mount.3mf
68.0 x 72.2 x 20.0 mm

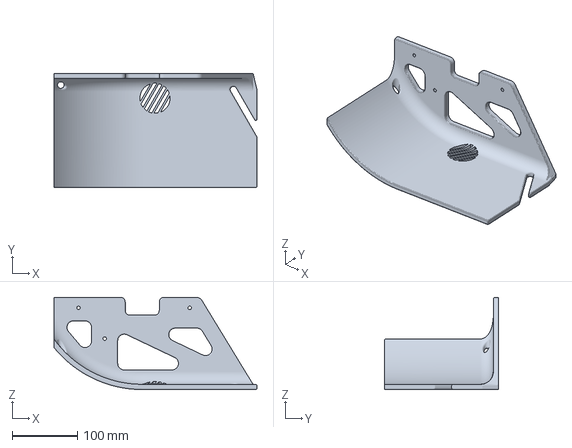
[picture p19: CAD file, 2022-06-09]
3MFs STLs/Electronics_Bay/Separation/Bay_Separation_Right_Part.3mf
310.5 x 175.0 x 141.0 mm

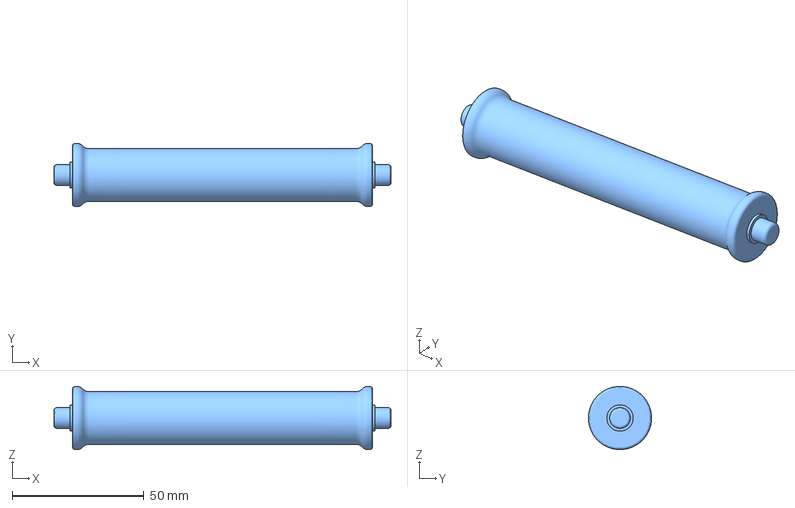
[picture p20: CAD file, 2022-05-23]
3MFs STLs/Electronics_Bay/Spool_Holder/a_FillerRollerSource_Dynasty_Remix.3mf
128.0 x 24.0 x 24.0 mm

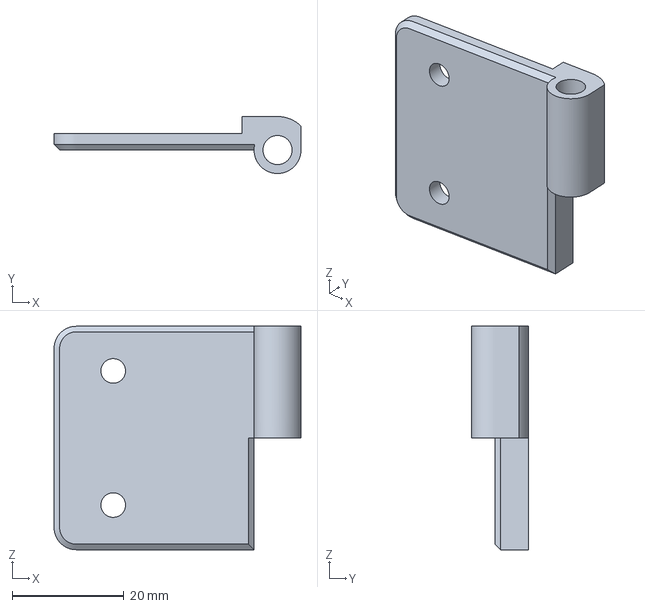
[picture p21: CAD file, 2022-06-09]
3MFs STLs/Enclosure/Door/Right_Door_Hinge_Door_Part.3mf
44.2 x 10.2 x 40.0 mm

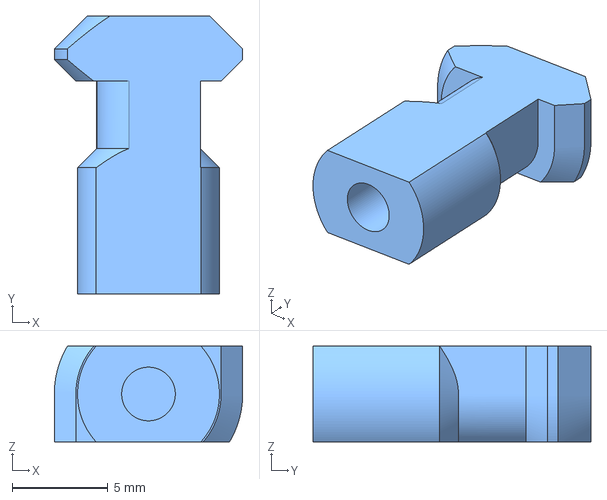
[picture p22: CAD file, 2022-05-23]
3MFs STLs/Enclosure/Door/Voron_Door_Latch_Remix/a_Enclosure_Latch_Right_Dynasty_Remix_x2.3mf
9.82 x 14.5 x 5.00 mm

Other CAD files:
3MFs STLs/Enclosure/Electronic_Panel/TPU_Grommet_30x4mm_x3.3mf
3MFs STLs/Enclosure/VzBoT_Handle_Dynasty_Remix_x2.3mf
3MFs STLs/EVA2_Hotend/EVA2_BLTouch/bl_touch_mount.3mf
3MFs STLs/EVA2_Hotend/EVA2_Dragon_Face/a_shroud_dynasty_remix.3mf
3MFs STLs/EVA2_Hotend/EVA2_BLTouch/bl_touch_mount.stl
3MFs STLs/EVA2_Hotend/EVA2_Dragon_Face/a_shroud_dynasty_remix.stl
3MFs STLs/EVA2_Hotend/EVA2_Dragon_Face/dragon_face.3mf
3MFs STLs/EVA2_Hotend/EVA2_Dragon_Face/dragon_face.stl
3MFs STLs/EVA2_Hotend/EVA2_Dragon_Face/v6_support.3mf
3MFs STLs/EVA2_Hotend/EVA2_Dragon_Face/v6_support.stl
3MFs STLs/EVA2_Hotend/EVA2_Endstop/top_endstop_openbuilds.3mf
3MFs STLs/EVA2_Hotend/EVA2_Endstop/top_endstop_openbuilds.stl
3MFs STLs/EVA2_Hotend/EVA2_Orbiter/a_Duct_v2.1_Straight.3mf
3MFs STLs/EVA2_Hotend/EVA2_Orbiter/a_Duct_v2.1_Straight.stl
3MFs STLs/EVA2_Hotend/EVA2_Orbiter/a_back_corexy.3mf
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

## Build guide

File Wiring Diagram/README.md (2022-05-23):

# Wiring Diagram

Electronics Wiring Diagram
Dynasty_Wiring_Diagram.

Electronics Block Diagram
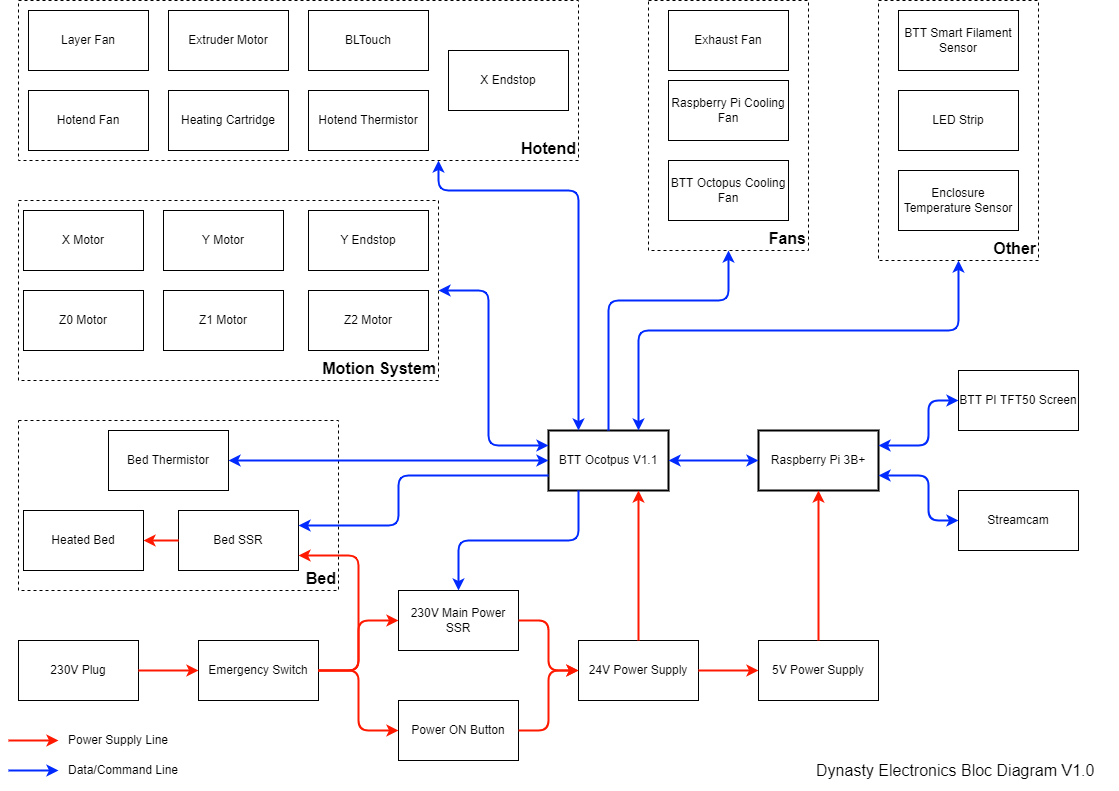
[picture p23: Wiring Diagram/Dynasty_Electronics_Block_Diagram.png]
Dynasty_Electronics_Block_Diagram


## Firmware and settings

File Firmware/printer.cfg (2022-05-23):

###########################
# File Name: printer.cfg
# Creator: Icarus3D
# Creation Date: 01.11.2021
# Last Update: 28.03.2022
# Version: V2.6
###########################

# Configuration file for 3D printer Dynasty (Corey XY type) using Mainsail/Klipper
# Use a Raspberry Pi 3B+
# The Motherboard is a BTT Octopus V1.1 with MCU STM32F446 + 12 MHz crystal: https://www.aliexpress.com/item/1005002613363656.html?spm=a2g0s.9042311.0.0.27424c4d8Xz5KI
# Uses E3D High Torque Motor 0.9° on every axes: https://e3d-online.com/products/motors
# Uses Orbiter 1.5 from Trianglelab as extruder: https://fr.aliexpress.com/item/1005002029267359.html?spm=a2g0s.9042311.0.0.27426c37L7t42k

# Klipper Configuration reference: https://www.klipper3d.org/Config_Reference.html

# Tips: To use timelapse, add "TIMELAPSE_TAKE_FRAME" in layer change gcode of the slicer and add "TIMELAPSE_RENDER" in the end gcode

#####################################################################
#       Include
#####################################################################
[include macro.cfg]
[include timelapse.cfg]
#[include adxl345.cfg]          # ADXL345 accelerometer for resonance compensation


#####################################################################
#       00 Micro-controller configuration
#####################################################################
[mcu]
serial: /dev/serial/by-id/usb-Klipper_stm32f446xx_02002B000A50534841313020-if00
baud: 250000                    # Need to redo a makeconfig to change the baudrate


#####################################################################
#       01 Common kinematic settings
#####################################################################
# Side belt frequency 57Hz
[printer] 
kinematics: corexy
max_velocity: 300               # (mm/s)
max_accel: 3000                 # (mm/s^2)
#max_accel: 10000               # (mm/s^2) ADXL345 accelerometer for resonance compensation
max_accel_to_decel: 3000        # (mm/s^2) Default is half of max_accel
#max_accel_to_decel: 10000      # (mm/s^2) ADXL345 accelerometer for resonance compensation
square_corner_velocity: 5.0     # (mm/s)
max_z_velocity: 20              # (mm/s)
max_z_accel: 200                 # (mm/s^2)


##--------------------------------------------------------------------
#       X/Y Stepper Settings
##--------------------------------------------------------------------
# Home postion (0,0) is at the front left corner of the printing surface.
#
#(-6.93,324.491)            (329.602,324.491)
#
#       (0,310)---------(310,310)
#       |                       |
#       |                       |
#       |                       |
#       |                       |               Y
#       |                       |               ^
#       (0,0)-------------(310,0)               |-> X
#
#(-6.93,-25.5)              (329.602,-25.5)
#
# Color patern stepper cable: Red = A1|/A, Blue = A2|A, Green = B2|B, Black = B1|/B
#
# Back left motor (A) connected at DRIVER0/MOTOR0 (PF13, PF12, !PF14) with Endstop connected at DIAG0 (^PG6)
[stepper_x]
step_pin: PF13
dir_pin: !PF12
enable_pin: !PF14
rotation_distance: 40           # (mm) rotation_distance = <belt_pitch> * <number_of_teeth_on_pulley> = 2*20 = 40
microsteps: 64
full_steps_per_rotation: 400    # 0.9 degree motor = 400
#gear_ratio:
#step_pulse_duration:
endstop_pin: ^PG6
position_min: -9             # (mm) 3d measure = -6.93
position_endstop: -9         # (mm) 
position_max: 325            # (mm) 3d measure = 329.602, was 327.5
homing_speed: 40.0              # (mm/s)
#homing_retract_dist: 5.0        # (mm)
#homing_retract_speed:          # (mm/s) The default is homing speed
#second_homing_speed:           # (mm/s) The default is homing_speed/2.
#homing_positive_dir:           # The default is true if position_endstop is near position_max and false if near position_min.

[tmc2209 stepper_x]
uart_pin: PC4
#tx_pin:
#select_pins:
interpolate: False            # Introduce small systemic positional error
run_current: 0.800              # Motor rated current DC 1.68A / Phase
#hold_current: 0.500            # Not recommended, introduce positon error
#sense_resistor: 0.110
#stealthchop_threshold: 0        # Disable
#uart_address: 0
#...

# Back Right motor (B) connected at DRIVER1/MOTOR1 (PG0, PG1, !PG15) with Endstop connected at DIAG1 (^PG9)
[stepper_y]
step_pin: PG0
dir_pin: !PG1
enable_pin: !PF15
rotation_distance: 40           # (mm) rotation_distance = <belt_pitch> * <number_of_teeth_on_pulley> = 2*20 = 40
microsteps: 64
full_steps_per_rotation: 400    # 0.9 degree motor = 400
#gear_ratio:
#step_pulse_duration:
endstop_pin: ^PG9
position_min: -25.5             # (mm) 3d measure = -25.5
position_endstop: 324.5         # (mm) 3d measure = 324.491
position_max: 324.5           # (mm) 3d measure = 324.491
homing_speed: 40.0               # (mm/s)
#homing_retract_dist: 5.0        # (mm)
#homing_retract_speed:          # (mm/s) The default is homing speed
#second_homing_speed:           # (mm/s) The default is homing_speed/2.
#homing_positive_dir:           # The default is true if position_endstop is near position_max and false if near position_min.

[tmc2209 stepper_y]
uart_pin: PD11
#tx_pin:
#select_pins:
interpolate: False            # Introduce small systemic positional error
run_current: 0.800              # Motor rated current DC 1.68A / Phase
#hold_current: 0.500            # Not recommended, introduce positon error
#sense_resistor: 0.110
#stealthchop_threshold: 0        # Disable
#uart_address: 0
#...

##--------------------------------------------------------------------
#       Z Stepper Settings
##--------------------------------------------------------------------
#
#   Y       |-----------------(Z2)
#   ^       |                   |
#   |-> X   |                   |
#           |                   |
#         (Z0)                  |
#           |                   |
#           |                   |
#           |                   |
#           |-----------------(Z1)
#
# Left Z Motor (Z0) connected at DRIVER2/MOTOR2 (PF11, PG3, !PG5) with BLtouch
[stepper_z]
step_pin: PF11
dir_pin: PG3
enable_pin: !PG5
rotation_distance: 8            # (mm) rotation_distance = <screw_pitch> * <number_of_separate_threads> = 2*4 = 8
microsteps: 16
full_steps_per_rotation: 400    # 0.9 degree motor = 400
#gear_ratio:
#step_pulse_duration:
#endstop_pin: ^PG10
endstop_pin: probe:z_virtual_endstop
position_min: 0                 # (mm)
#position_endstop: 0            # (mm)
position_max: 360               # (mm)
#homing_speed: 5.0               # (mm/s)
#homing_retract_dist: 5.0        # (mm)
#homing_retract_speed:          # (mm/s) The default is homing speed
#second_homing_speed:           # (mm/s) The default is homing_speed/2.
#homing_positive_dir:           # The default is true if position_endstop is near position_max and false if near position_min.

[tmc2209 stepper_z]
uart_pin: PC6
#tx_pin:
#select_pins:
interpolate: False            # Introduce small systemic positional error
run_current: 0.800              # Motor rated current DC 1.68A / Phase
#hold_current: 0.500            # Not recommended, introduce positon error
#sense_resistor: 0.110
#stealthchop_threshold: 0        # Disable
#uart_address: 0
#...

# Right Front Z Motor (Z1) connected at DRIVER3/MOTOR3 (PG4, PC1, !PA0)
[stepper_z1]
step_pin: PG4
dir_pin: PC1
enable_pin: !PA0
rotation_distance: 8            # (mm) rotation_distance = <screw_pitch> * <number_of_separate_threads> = 2*4 = 8
microsteps: 16
full_steps_per_rotation: 400    # 0.9 degree motor = 400
#endstop_pin: ^PG11

[tmc2209 stepper_z1]
uart_pin: PC7
#tx_pin:
#select_pins:
interpolate: False            # Introduce small systemic positional error
run_current: 0.800              # Motor rated current DC 1.68A / Phase
#hold_current: 0.500            # Not recommended, introduce positon error
#sense_resistor: 0.110
#stealthchop_threshold: 0        # Disable
#uart_address: 0
#...

# Right Back Z Motor (Z2) connected at DRIVER4/MOTOR4 (PF9, PF10, !PG2)
[stepper_z2]
step_pin: PF9
dir_pin: PF10
enable_pin: !PG2
rotation_distance: 8            # (mm) rotation_distance = <screw_pitch> * <number_of_separate_threads> = 2*4 = 8
microsteps: 16
full_steps_per_rotation: 400    # 0.9 degree motor = 400
#endstop_pin: ^PG12

[tmc2209 stepper_z2]
uart_pin: PF2
#tx_pin:
#select_pins:
interpolate: False            # Introduce small systemic positional error
run_current: 0.800              # Motor rated current DC 1.68A / Phase
#hold_current: 0.500            # Not recommended, introduce positon error
#sense_resistor: 0.110
#stealthchop_threshold: 0        # Disable
#uart_address: 0
#...
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

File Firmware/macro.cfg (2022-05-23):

###########################
# Creator: Icarus3D
# Creation Date: 01.11.2021
# Last Update: 04.03.2022
# Version: V2.1
###########################

# Mainsail Doc: https://docs.mainsail.xyz/
# Klipper gcode: https://www.klipper3d.org/G-Codes.html
# Klipper command: https://www.klipper3d.org/Command_Templates.html
# jinja template: https://jinja.palletsprojects.com/en/3.0.x/templates/

# Tips: Prefixing the name with an underscore hide the macro on the interface

#####################################################################
#        G-Code macros and events
#####################################################################
#----------------------------------------
#       START & END SCRIPT
#----------------------------------------

# Maybe usefull with start gcode:
;SET_VELOCITY_LIMIT VELOCITY=350 ACCEL=5000 ACCEL_TO_DECEL=5000 SQUARE_CORNER_VELOCITY=5
;SET_PRESSURE_ADVANCE EXTRUDER=extruder ADVANCE=0.048 SMOOTH_TIME=0.04
;SET_FILAMENT_SENSOR SENSOR=smart_filament_sensor ENABLE=1
;START_PRINT T_BED={temperature_heatbed} T_EXTRUDER={temperature_extruder1}

# Print start script preheating the nozzle above the purge bucket and wiping it with the brush
# Declaration: START_PRINT T_BED=<temperature(°C)> T_EXTRUDER=<temperature(°C)>
# Example: START_PRINT T_BED=60 T_EXTRUDER=205
# Example CURA: START_PRINT T_BED={material_bed_temperature_layer_0} T_EXTRUDER={material_print_temperature_layer_0}
# Example SIMPLIFY3D: START_PRINT T_BED=[bed0_temperature] T_EXTRUDER=[extruder0_temperature]
[gcode_macro START_PRINT]
description: Startup script, preheating hotend above purge bucket
gcode:
    CLEAR_PAUSE                         # Clears the current paused state without resuming the print
    G90                                 # Absolute positioning
    M82                                 # Extruder absolut
    M106 S0                             # Fan off
    G28                                 # Home all axes
    Z_TILT_ADJUST                       # Do a z tilt to ajust the bed
    BED_MESH_PROFILE LOAD=default       # Load bed mesh
    G0 X-5.00 Y0.00 F3600               # Move nozzle near purget backet at 60mm/s
    G0 Z1.00 F600                       # Raise the bed after the z tilt
    M400                                # Wait for current moves to finish
    G0 X-5.00 Y-24.00 F3600             # Move nozzle above purget backet at 60mm/s
    SET_LED LED=light_hotend RED=0.56 GREEN=0.00 BLUE=1.00 WHITE=0.00   # Set neopixel violet
    #M117 Start preheating               # Message
    M104 S140                           # Set preheat hotend
    M190 S{params.T_BED}                # Set preheat bed and wait
    SET_LED LED=light_hotend RED=1.00 GREEN=0.00 BLUE=0.00 WHITE=0.00   # Set neopixel red
    M109 S{params.T_EXTRUDER}           # Set preheat hotend and wait
    SET_LED LED=light_hotend RED=0.00 GREEN=0.00 BLUE=0.00 WHITE=0.40   # Set neopixel white
    G92 E0                              # Zero the extruder
    G1 E10.0 F150                        # Extrude 10mm at 2.5mm/s
    M400                                # Wait for current moves to finish
    G92 E0                              # Zero the extruder
    G0 X35.00 Y-24.00 F3600             # Brush nozzle 3 times at 60mm/s
    G0 X25.00 Y-24.00 F3600 
    G0 X35.00 Y-24.00 F3600
    G0 X25.00 Y-24.00 F3600
    G0 X35.00 Y-24.00 F3600
    G0 X25.00 Y-24.00 F3600
    #M117 Start print                    # Message

# Print ending script
# Example: END_PRINT AUTO_SHUTDOWN=True
[gcode_macro END_PRINT]
description: End script, Move hotend, turn off heater, motor and power down printer 
gcode:
    ##### set auto_shutdown default #####
    {% set auto_shutdown = params.AUTO_SHUTDOWN|default(false) %}
    ##### end of definitions #####
    M400                           # Wait for current moves to finish
    G91                            # Relative positioning
    G0 X5.00 Y5.00 Z5.00 F3600      # Move nozzle up to remove stringing at 60mm/s
    G92 E0                         # Zero the extruder
    G1 E-1 F2400                 # Retract filament by 1mm at 40mm/s
    TURN_OFF_HEATERS
    SET_LED LED=light_hotend RED=0.00 GREEN=0.00 BLUE=1.00 WHITE=0.00   # Set neopixel blue
    M107                           # Turn off fan
    SET_FAN_SPEED FAN=exhaust_fan SPEED=0.0  # Turn off exaust fan
    G90                            # Absolute positioning
    G0 X155 Y310 F3600             # Park nozzle to the rear center at 60mm/s
    #G0 X-4 Y-20 F3600             # Park nozzle to the front left at 60mm/s
    M400                            # Wait for current moves to finish
    M84                            # Turn off all motors
    TIMELAPSE_RENDER                # Render timelapse
    {% if auto_shutdown == "true" or auto_shutdown == "True" %}
        M117 Printer will shutdown when the hotend reaches 50C      # Message
        RESPOND PREFIX=tgalarm_photo MSG="Finished printing. Printer will shutdown when the hotend reaches 50C"
        TEMPERATURE_WAIT SENSOR=extruder MAXIMUM=50 # Wait until the hotend temp drops below 50°C
        RESPOND PREFIX=tgnotify MSG="Printer power off"
        G4 P5000                                    # Wait 5sec to send notify
        SET_PIN PIN=power_supply VALUE=0            # Shutdown the printer
    {% else %}
        M117 Printing finished      # Message
        RESPOND PREFIX=tgalarm_photo MSG="Finished printing"
    {% endif %}


#----------------------------------------
#       FILAMENT
#----------------------------------------
# Distance between nozzle and extruder gear = 97mm
# Distance between nozzle and top orbiter = 126mm
# Distance between start heatbreak and top extruder gear = 58m
# Distance from the nozzle tip to the PTFE end = 90mm
# Warning!: With the unload macro, do not exceed the distance of the extruder gears that may crush the filament
[gcode_macro UNLOAD_FILAMENT]
description: Unload the filament just before the gears
gcode:
    SAVE_GCODE_STATE NAME=unload_filament_state
    M83                            # Set extruder to relative
    G1 E5 F300                    # Extrude a little to soften tip at 5mm/s
    G1 E-66 F2400                 # Retract filament completely at 40mm/s
    #M84 E0                       # Disable extruder stepper
    RESTORE_GCODE_STATE NAME=unload_filament_state

[gcode_macro LOAD_FILAMENT]
description: Load the filament and purge a little
gcode:
    SAVE_GCODE_STATE NAME=load_filament_state
    M83                            # Set extruder to relative
    G1 E60 F1200                  # Quickly load filament to down bowden at 20mm/s
    G1 E50 F300                    # Slower extrusion for hotend path at 5mm/s
    G1 E15 F150                    # Prime nozzle with filament at 2.5mm/s
    RESTORE_GCODE_STATE NAME=load_filament_state

# Change filament
[gcode_macro M600]
description: Change filament, use PAUSE macro
gcode:
    ##### read E from pause macro #####
    {% set E = printer["gcode_macro PAUSE"].extrude|float %}
    ##### set x,y,z default #####
    {% set X = params.X|default(155)|float %}
    {% set Y = params.Y|default(-24)|float %}
    {% set Z = params.Z|default(10)|float %}
    ##### end of definitions #####
    SAVE_GCODE_STATE NAME=M600_state
    PAUSE
    G91                         # Relative coordinates
    G1 Z{Z}
    G90                         # Absolute coordinates
    G1 X{X} Y{Y} F3000
    G91                         # Relative coordinates
    G1 E{E} F1800               # Extrud 1.6mm at 30mm/s
    G1 E-80 F2400              # Retract extruder 80mm at 40mm/s
    RESTORE_GCODE_STATE NAME=M600_state

# Filament detector runout macro
[gcode_macro FILAMENT_RUNOUT]
description: Macro called when the filament detector detects an error
gcode:
    M117 Pause called by the filament sensor
    RESPOND PREFIX=tgalarm_photo MSG="Pause called by the filament sensor"


#----------------------------------------
#       SHORTCUT
#----------------------------------------
# Save actual configuration in printer.cfg
[gcode_macro CONFIG_SAVE]
gcode:
    SAVE_CONFIG

# Power down printer with the main SSR
[gcode_macro POWER_OFF]
gcode:
    SET_PIN PIN=power_supply VALUE=0

# Turn off neopixel
[gcode_macro LIGHT_OFF]
gcode:
    SET_LED LED=light_hotend RED=0.00 GREEN=0.00 BLUE=0.00 WHITE=0.00

# Turn on only withe neopixel
# Example: LIGHT_ON RED=1.0 GREEN=0.0 BLUE=0.0 WHITE=0.0
[gcode_macro LIGHT_ON]
gcode:
    ##### end of definitions #####
    {% set red = params.RED|default(0.0)|float %}
    {% set green = params.GREEN|default(0.0)|float %}
    {% set blue = params.BLUE|default(0.0)|float %}
    {% set white = params.WHITE|default(1.0)|float %}
    ##### end of definitions #####
    #SET_LED LED=light_hotend RED=0.00 GREEN=0.00 BLUE=0.00 WHITE=1.00
    SET_LED LED=light_hotend RED={red} GREEN={green} BLUE={blue} WHITE={white}

# Disable all stepper motors
[gcode_macro DISABLE_MOTORS]
gcode:
    M84
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

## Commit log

2022-05-23 Inital Commit
    [Back_3D_Panel_Part1.3mf, Back_3D_Panel_Part1.stl, Back_3D_Panel_Part2.3mf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]
2022-06-09 Add STLs sepration bay
    [Bay_Separation_Left_Part.3mf, Bay_Separation_Left_Part.stl, Bay_Separation_Right_Part.3mf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]
2022-06-09 Relocate files
    [Bay_Separation_Left_Part.3mf, Bay_Separation_Left_Part.stl, Bay_Separation_Right_Part.3mf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]
2022-06-10 Update CAD
